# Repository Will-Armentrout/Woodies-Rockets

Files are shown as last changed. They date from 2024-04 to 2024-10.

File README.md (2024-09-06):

# Woodies-Rockets
All files related to rocket design and control\
Created by Will A., Cole D., and Matthew P.\
**How to make a rocket by three college kids** \
Give us a follow at @GoodEnuffEngineering on YouTube, or take the [link](https://www.youtube.com/channel/UCJkPznxXx-ik1TMp3VLUVOw)\
All Scheduling and Daily updates will be listed at the notion linked [here](https://imaginary-cadmium-d3f.notion.site/Woodies-Wockets-60ab52ea17414d15b66bf4899e530979?pvs=4)

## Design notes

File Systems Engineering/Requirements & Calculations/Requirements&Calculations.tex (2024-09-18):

\documentclass[12pt, letter paper]{article}

\usepackage[a4paper, left=0.9in, right=0.9in, top=1in, bottom=1in]{geometry}
\usepackage{graphics}
\usepackage[colorlinks=true, linkcolor=blue, urlcolor=blue]{hyperref}
\usepackage{gensymb}

\title{Requirements and Calculations of a Liquid Rocket Engine}
\author{Will Armentrout}
\date{September 15, 2024}

\begin{document}
	\maketitle

	\tableofcontents
	
	\section{Nomenclature and Terms}
		$ N2O $ - Nitrous Oxide \\
		$ IPA $ - Isopropyl Alcohol \\
		$I_{sp}$ - Specific Impulse\\
		$ O/F $ - Oxidizer/Fuel Ratio
		
	\section{System Requirements/Specifications}
	\begin{center}
		\begin{tabular}{|c |c |c |}
			\hline
			\textbf{Requirement} & \textbf{Value} & \textbf{From?} \\ \hline
			Thrust & 900 N & Rocket Weight \\ \hline
			Specific Impulse & 226 s & NASA CEA \\ \hline
			Tank Pressure & 5.127 MPa & Property (Vapor Pressure: 20 C) \\ \hline
			O/F Mole Ratio & 9 & Ideal Reaction \\ \hline
			O/F Mass Ratio & 6.6 & Calculated (O/F Mole Ratio) \\ \hline 
			Weight Flow Rate & 3.6 N/s & Calculated (Thrust and Isp)\\ \hline
			Mass Flow Rate & 0.4059 kg/s & Calculated (Weight Flow Rate) \\ \hline
			Ox Mass Flow Rate & 0.3525 kg/s & Calculated (Mass Flow Rate) \\ \hline
			Fuel Mass Flow Rate & 0.0534 kg/s & Calculated (Mass Flow Rate) \\ \hline
			Chamber Pressure & 3 MPa & Assumed (Tank Pressure) \\ \hline
			Chamber Temperature & 2966 K & NASA CEA \\ \hline
			Chamber Gas Density & 3.3349 kg/m3 & NASA CEA \\ \hline
			Chamber Gamma & 1.1459 & NASA CEA \\ \hline
			Chamber Mach Number & 0.00 & Assumption \\ \hline
			Chamber SoS & 1015 m/s & NASA CEA \\ \hline
			Throat Pressure & 1.7248 MPa & NASA CEA \\ \hline
			Throat Temperature & 2790 K & NASA CEA \\ \hline
			Throat Gas Density & 2.0577 kg/m3 & NASA CEA \\ \hline
			Throat Gamma & 1.1471 & NASA CEA \\ \hline
			Throat Mach Number & 1.00 & Definition \\ \hline
			Throat SoS & 981 m/s & NASA CEA \\ \hline
			Exit Pressure & 0.1 MPa & Estimated (Altitude) \\ \hline
			Exit Temperature & 1907 K & NASA CEA \\ \hline
			Exit Gas Density & 0.17948 kg/m3 & NASA CEA \\ \hline
			Exit Gamma & 1.2044 & NASA CEA \\ \hline
			Exit Mach Number & 2.708 & NASA CEA \\ \hline
			Exit SoS & 819 m/s & NASA CEA \\ \hline
			Area Ratio & 5.0683 & NASA CEA \\ \hline
			C* & 1487 m/s & NASA CEA \\ \hline
			Specific Gas Constant & 32.4638 g/mol & NASA CEA \\ \hline
			Throat Area & $ 65.591 mm^2 $ & Calculated (Isentropic Equations) \\ \hline
			Throat Diameter & 9.1385 mm & Calculated \\ \hline
			Exit Area & $ 332.4343 mm^2 $ & Calculated (Area Ratio) \\ \hline
			Exit Diameter & 20.5734 mm & Calculated \\ \hline
			Nozzle Exit Angle & 15\degree & Determined (Hobby Rocket Engines)\\ \hline
			Throat Entry Angle & 30\degree & Determined (Youngblood) \\ \hline
			Characteristic Length & 1 m & Determined (Youngblood) \\ \hline
			Chamber Diameter & 30 mm & Determined \\ \hline
			Chamber Length & 84.36 mm & Calculated (Hobby Rocket Engines) \\ \hline
			Chamber Wall Thickness & 5 mm & Calculated \& Determined \\ \hline

		\end{tabular}
	\end{center}

	\section{Derivations, Formulas \& Calculation Process}
		
		\subsection{Deriving Oxidizer/Fuel Ratio}
			Ideal Reaction: 
			$ C_3H_8O + 9N_2O \rightarrow 3CO_2 + 4H_2O + 9N_2 $ 
			\begin{center}
			\textbf{\textit{In reality the reaction is more complicated. the heat of reaction causes many radicals and exotic species that can be calculated but are ignored for simplicity.}} 
			\end{center}
			\noindent Mole O/F Ratio of 9 (9 Moles of N2O for 1 mole of C3H8O). \\
			$ M_{N2O} = 2*14 + 16 = 44 $, 
			$ M_{C3H8O} = 3*12 + 8*1 + 16 =60 $ \\ \\
			$O/F_{Mass} = \frac{9*44}{60} = 6.6 $ (6.6 kg of N2O for 1 kg of C3H8O)
		
		\subsection{NASA CEA}
			Once these variables have been determined the NASA CEA (Chemical Equalibrium with Applications) or other equalibrium solver can be used to get many other critical parameters.
			\subsubsection{Procedure for running the NASA CEA}
				This is by no means the only way to do it. This is also intended as an early design exercise where other chamber pressures and O/F ratios should be analyzed. 
				If you just want a single analysis point don't use the interval tabs and just use the number entry on the right side of the tabs for pressure and O/F ratio.
				\begin{enumerate}
					\item Look up NASA CEA on any browser. URL: \href{https://cearun.grc.nasa.gov/}{\underline{https://cearun.grc.nasa.gov/}}
					\item On the right hand side in the chemical equalibrium problem types check "Rocket". Then hit submit.
					\item On the "Pressure" tab (should be autoselected) enter values for the chamber pressure. 
						\begin{itemize}
							\item This will be based on the tank pressure (5.127 MPa) and the losses in the plumbing to the chamber. 
							\item Since MPa, isn't a selectable option, multiply the MPa number by 10 to get the pressure in bar.
							\item Assume 3 MPa as an approximate starting point. Since 3 MPa is our goal pressure, input 2 MPa (20 bar) as a Low Value and 5 MPa (50 bar) as a high value. 
							\item Make the interval smaller, maybe 0.5 MPa (5 bar) to see a range of pressure values. 
							\item Accept Input and Continue.
						\end{itemize}
					\item On the "Fuel(s)" tab check the "Use Periodic Table (mixtures)" since IPA isn't on the quick select list. Accept Fuel Selection and Continue.
					\item On the "Periodic Table" check Hydrogen, Carbon and Oxygen (as these are the component elements in IPA). Accept Element Selections and Continue.
					\item On the "Select your Fuel(s)" tab check C3H8O, 2propanol (This is the chemical formula and name for Isopropyl Alcohol). Accept Selected Reactant(s) and Continue. 
						There should be a confirmation form, Fuel Mix form and Component Properties form. Accept inputs for all and continue to the next form.
					\item On the "Select your Oxidizer(s)" tab check N2O. Accept Oxidizer Selection and Continue to the next form.
					\item On the "Enter proportions of Oxidizer/Fuel" on the top selection area select Specify with Oxidizer/Fuel Wt. Ratio. 
						\begin{itemize}
							\item We calculated the stoichometric O/F weight ratio earlier as being 6.6. 
							\item If 6.6 is the target value enter a low value of 4 and a high value of 8 and use an interval of 0.2.
						\end{itemize}
					\item On the "Define Exit Conditions" tab define Chamber/Exit Pressure Ratios on the left hand side. 
						\begin{itemize}
							\item In rocket engines the most efficient engine is one that is perfectly expanded (meaning the pressure at the exit of the nozzle is at ambient pressures).
							\item A rocket engine will fly in a multitude of different pressures as it travels upward (pressure decreases with altitude),
								but for now we will analyze with a exit pressure of 1 bar (or about 110m in altitude) as a baseline.
							\item In order to get an exit pressure of 1 bar we take our chamber pressure range (2-5 MPa in steps of 0.5 MPa or 20-50 bar in steps of 5 bar) and divide it by the desired exit pressure.
							\item So for this it's easy. The ratios are just the chamber pressure values. You will have to input each ratio manually (20, 25, 30 ... to 50) on the left column.
							\item Accept Input and Continue to Next Form.
						\end{itemize}
					\item On the "Enter Your Final Choices Before Running CEA" the autogenerated selections should be good (Short, Mass-Fractions, Equilibrium). 
						You can look at your entered ranges for chamber pressure, O/F ratio and chamber/exit pressure ratios before you run the CEA.
						Submit Input and Perform CEA Analysis.
					\item The CEA should run in less than a couple of seconds. The file displayed in the embedded window is the output file. You can download the input and output files in the top right.		
				\end{enumerate}
			\subsubsection{Procedure for analyzing the NASA CEA output}
				The output file of the NASA contains many valuable pieces of information that will be useful in designing a rocket engine later. 
				A navigation tip: the CEA output file is sorted from smallest to largest O/F ratio first and within each O/F ratio it is sorted by chamber pressure. 
				\begin{enumerate}
					\item Scroll through the output file to find the O/F Ratio of 6.6 and the Pin of 3 MPa (435.1 psi). For some reason the CEA output only displays the chamber pressures in psi no matter the input unit.
					\item Once you have found the section where Pin = 435.1 psi and O/F = 6.6 find the exit condition where the P, bar equals 1.000 or Pinf/P = 30. 
						\begin{itemize}
							\item The chamber, throat and exit pressure column where P, BAR = 1.000 (or another exit pressure) are the only columns of interest per section.
						\end{itemize}
					\item Find and record the variables of interest.
						In our case this would be pressure (P), temperature (T), density (RHO), mach number, specific heat ratio (GAMMA), speed of sound (SON VEL), area ratio (Ae/At),
						c star, specific impulse (Isp) and the mass fractions. Here are the values:
						\begin{itemize}
							\item Pressure at the throat: 17.248 Bar
							\item Temperature in the combustion chamber: 2966 K, throat: 2790 K, exit: 1907 K
							\item Density of the combustion gases in the combustion chamber: 3.3349 kg/m3, throat 2.0577 kg/m3, exit 0.17948 kg/m3
							\item Mach Number at exit: 2.708
							\item Specific Heat Ratio at the combustion chamber: 1.1459, throat: 1.1471, exit: 1.2044
							\item Speed of Sound at the combustion chamber: 1015 m/s, throat: 981 m/s, exit: 819 m/s
							\item Area Ratio: 5.0683
							\item C star: 1487 m/s
							\item Specific Impulse: 2218 m/s. In order to convert this to the familiar specific impulse with units of seconds divide by the gravitational constant g = 9.81. $ I_{sp} = \frac{2218}{9.81} = 226 s $
							\item The mass fractions are listed for the main combustion gas products.
							\begin{itemize}
								\item CO: Combustion Chamber - 0.05069, Throat -  0.03951, Exit - 0.00258
								\item CO2: Combustion Chamber - 0.20943, Throat - 0.22700, Exit - 0.28503
								\item H: Combustion Chamber - 0.00010, Throat -  0.00007, Exit - 0.00000
								\item HO2: Combustion Chamber - 0.00003, Throat - 0.00002, Exit - 0.00000
								\item H2: Combustion Chamber - 0.00083, Throat - 0.00065, Exit - 0.00006
								\item H2O: Combustion Chamber - 0.14328, Throat - 0.14690, Exit - 0.15703
								\item NO: Combustion Chamber - 0.01266, Throat - 0.00909, Exit - 0.00047
								\item NO2: Combustion Chamber - 0.00002, Throat - 0.00001, Exit - 0.00000
								\item N2: Combustion Chamber - 0.54681, Throat - 0.54849, Exit - 0.55252
								\item O: Combustion Chamber - 0.00151, Throat - 0.00093, Exit - 0.00001
								\item OH: Combustion Chamber - 0.01160, Throat - 0.00850, Exit - 0.00041
								\item O2: Combustion Chamber - 0.02302, Throat -  0.01885, Exit - 0.00190
							\end{itemize}
						\end{itemize}
				\end{enumerate}
			
		\subsection{Deriving the Flow rates}
			Specific Impulse Equation:  $I_{sp} = \frac{T}{\dot{m} g_0} $ 
			$\rightarrow$
			Weight Flow Version: $ \dot{W} = \dot{m} g_0= \frac{T}{I_{sp}}$ \\
			Solve: $ \dot{W} = \frac{900 N}{226 s} = 3.982 N/s $ \\ \\
			Convert to mass flow: $ \dot{m} = \frac{\dot{W}}{g_0} \rightarrow \dot{m} = \frac{3.9823}{9.81} = 0.4059 kg/s $ \\ \\
			Separate into oxidizer and fuel mass flow rates: \\
			Oxidizer - Nitrous Oxide: $ \dot{m}_{N2O} = \dot{m} * \frac{6.6}{7.6} = 0.3525 kg/s $ \\
			Fuel - Isopropyl Alcohol: $ \dot{m}_{IPA} = \dot{m}*\frac{1}{7.6} = 0.0534 kg/s $ \\
	
	\section{Design Equations}
		\subsection{Nozzle Design Equations}
			\subsubsection{Solving for the specific gas constant}
				The Univeral Gas Constant $ \bar{R} $ is 8.314 J/molK. \\
				The specific gas constant is $ R = \frac{\bar{R}}{M} $ where M is the molecular weight of the mixture of product gases.
				Need to solve for the molecular weight of all of the component gases and their moles in mass fraction.
				\begin{itemize}
					\item CO: $ M = 12 +16 = 28 $ $x_{CO} = 28 \cdot 0.03951 = 1.1063 $ moles
					\item CO2: $ M = 12 + 16  + 16 = 44 $ $ x_{CO2} = 44 \cdot 0.2270 = 9.988 $ moles
					\item H: $ M = 1 $ $ x_{H} = 1 \cdot 0.00007 = 0.00007 $ moles
					\item HO2: $ M = 1 + 16 + 16 = 33 $ $ x_{HO2} = 33 \cdot 0.00002 = 0.00066 $ moles
					\item H2: $ M = 1 + 1 = 2 $ $ x_{H2} = 2 \cdot 0.00065 = 0.0013 $ moles
					\item H2O: $ M = 1 + 1 + 16 = 18 $ $ x_{H2O} = 18 \cdot 0.1469 = 2.6442 $ moles
					\item NO: $ M = 14 + 16 = 30 $ $ x_{NO} = 30 \cdot 0.00909 = 0.2727 $ moles
					\item NO2: $ M = 14 + 16 + 16 = 46 $ $ x_{NO2} = 46 \cdot 0.00001 = 0.00046 $ moles
					\item N2: $ M = 14 + 14 = 28 $ $ x_{N2} = 28 \cdot 0.54849 = 15.3577 $ moles
					\item O: $ M = 16 $ $ x_{O} = 16 \cdot 0.00093 = 0.01488 $ moles
					\item OH: $ M =16 + 1 = 17 $ $ x_{OH} = 17 \cdot 0.0085 = 0.1445 $ moles
					\item O2: $ M =16 + 16  = 32 $ $ x_{O2} = 32 \cdot 0.01885 = 0.6032 $ moles
					\item Total: $ x_{total} = 1.1063 + 9.988 + 0.00007 + 0.00066 + 0.0013 + 2.6442 + 0.2727 + 0.00046 + 15.3577 + 0.01488 + 0.1445 +0.6032 = 30.1346 $ moles
				\end{itemize}
				Molecular weight of mixture is $M = 28 \cdot \frac{1.1063}{30.1346} + 44 \cdot \frac{9.988}{30.1346} + 1 \cdot \frac{0.00007}{30.1346} + 33 \cdot \frac{0.00066}{30.1346} + 2 \cdot \frac{0.0013}{30.1346} + 18 \cdot \frac{2.6442}{30.1346} + 30 \cdot \frac{0.2727}{30.1346} + 46 \cdot \frac{0.00046}{30.1346} + 28 \cdot \frac{15.3577}{30.1346} + 16 \cdot \frac{0.01488}{30.1346} + 17 \cdot \frac{0.1445}{30.1346} + 32 \cdot \frac{0.6032}{30.1346} = 32.4645 g/mol$ \\ \\
				Solve for specific gas constant $ R = \frac{8.314}{32.4645} = 0.2561 J/gK = 256.1 J/kgK $ 

			\subsubsection{Throat Area}
				Mass Flow Rate at the throat: $ \dot{m} = A_t \frac{P_o}{\sqrt{T_o}}\sqrt{\frac{\gamma}{R}} (\frac{\gamma + 1}{2})^{\frac{\gamma + 1}{2(1-\gamma)}}  $ \\
				Area of Throat: $ A_t = \frac{\dot{m}\sqrt{T_o}}{P_o}\sqrt{\frac{R}{\gamma}} (\frac{\gamma + 1}{2})^{\frac{\gamma + 1}{2(\gamma -1)}}$ \\ \\
				Values used in the Equation: \\
				Mass Flow Rate $ \dot{m} = 0.4059 kg/s $ \\
				Stagnation Temperature $ T_o = T_{chamber} = 2966 K $ \\
				Stagnation Pressure $ P_o = P_{chamber} = 3 MPa $ \\
				Gamma (at the throat) $ \gamma_{throat} = 1.1471 $ \\
				Specific Gas Constant (at the throat) $ R_{throat} = 256.1 J/kgK $ \\ \\
				Plug in the numbers: $ A_t = \frac{0.4059 \cdot \sqrt{2966}}{3 \cdot 10^6}\sqrt{\frac{256.1}{1.1471}} (\frac{1.1471 + 1}{2})^{\frac{1.1471 + 1}{2(1.1471 -1)}} = 6.5591 \cdot 10^{-5} m^2$ \\ \\
				Solve for Diameter $ A_t = \pi \frac{{D_t}^2}{4}  \rightarrow D_t = \sqrt{\frac{4A_t}{\pi}} = \sqrt{\frac{4 \cdot (6.5591 \cdot 10^{-5})}{\pi}} = 0.0091385 m = 9.1385 mm$
			
			\subsubsection{Exit Area}
				Use the throat area and determined $ A_e/A_t $ to get the exit area. $ \frac{A_e}{A_t} = 5.0683 $ \\
				$ A_e = 5.0683 \cdot 6.5591 \cdot 10^{-5} = 3.3243 \cdot 10^{-4} m^2$ \\
				Diameter: $ D_e = \sqrt{\frac{4 A_e}{\pi}} = \sqrt{\frac{4 \cdot(3.3243 \cdot 10^{-4})}{\pi}} = 0.02057 m = 20.5734 mm $ \\
			
			\subsubsection{Nozzle Angles}
				In normal commercial rocket engines the nozzle angle is optimized so that when the flow leaves it is as 1D as possible, to achieve max thrust. 
				The profile that maximizes thrust for a certain throat area and length is called an "Rao optimum contour". This is is named after G.V.R Rao and is complicated to manufacture. 
				Because of its complexity we will just use a 15{\degree} conical nozzle profile, common for hobby and small area ratio engines. It has 98.3\% of the performance of an ideal nozzle, so close enough for me.

		\subsection{Combustion Chamber Equations}
			
			\subsubsection{Chamber Length}
				For the combustion chamber Hobby Rocket Engines references a combustion chamber with a cross sectional area of at least 3 times the throat area. 
				For this reason we choose a chamber diameter of 30 mm, much larger than the required size, subject to change based on the injector. \\ \\
				The chamber volume required for complete combustion is defined by the characteristic chamber length: $ L^* = V_c/A_t \rightarrow L^* A_t = V_c $ where $ V_c = A_c L_c +$ convergent volume  \\
				Youngblood references a characterisitc length of 1m being successful in nitrous, ethanol engines so that value will be used as a minimum. \\ \\
				For small combustion chambers the convergent volume is 1/10th the cylindrical portion so $V_c = 1.1A_cL_c $ \\
				Combine Equations $ L^* A_t = 1.1A_cL_c \rightarrow L_c = \frac{L^* A_t}{1.1A_c} = \frac{(1) (6.5591 \cdot 10^{-5})}{1.1(\pi \frac{0.03^2}{4})} = 0.08436 m$ or $ 84.36 mm $
			
			\subsubsection{Chamber Thickness}
				This system will definitely not be thin walled but it is a good starting point for minimums. \\
				The axial or longnitudinal stress in a thin walled pressure vessel is given by the equation: 
				$ \sigma_a = \frac{Pr}{2t} $ Where P is the pressure, r is radius and t is the thickness. \\ \\
				Rrearrange for thickness: $ t = \frac{Pr}{2\sigma_a} $ In our case pressure is the chamber pressure (3 MPa), radius is 15 mm and sigma is material dependent. 
				Since steel is cheap we will use that, heat transfer be damned (hopefully we don't run it for long enough). Steel rod stock on McMaster has a tensile yield stress of 60,000 psi or 413.685 MPa. \\
				Plug this in:  $ t = \frac{3 \cdot 15}{2 \cdot 413.685} = 0.054389 mm $ 
				Remember this number is at ambient temperatures and the combustion chamber gas were calculated to be at 2966 K (Above the melting point of steel). \\ \\
				Recalculating with an operating temperature of 500{\degree}C or 773.15 K steel has about 40\% of it's yield strength at 21C. Using this: $ t = \frac{3 \cdot 15}{2 \cdot(0.4) (413.685) \cdot} = 0.13597 mm $ \\
				Not really much of a worry, but let's use something thick enough to handle the heat loads as well, call the wall thickness 5mm.

\end{document}

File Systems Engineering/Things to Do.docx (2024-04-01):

# Things to Do

1. Determine Thrust, Specific Impulse, Flow Rate
2. Propellant Determination
  a. Stoichiometric Ratio
3. Run CEA
  a. Get O/F
  b. Combustion Temperature
  c. Exit Velocity
  d. Area Ratio
  e. Combustion Pressure
  f. Gamma
4. Design Nozzle and Combustion Chamber
5. Research Injector Types, Determine optimal injector design.
6. Design Injector Plate
7. Flow Diagram
  a. Determine Fuel/Ox and Backfill Gas Tanks
  b. Gas Hose
  c. Valves
  d. Connectors
  e. Gauges
8. Design a Test Stand
  a. Aluminum Extrusion
  b. Force Transducer
  c. SAFETY
9. Find a place to test this.
10. Test

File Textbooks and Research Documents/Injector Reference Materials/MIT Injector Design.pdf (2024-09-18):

Created by Unknown User (ahodge@mit.edu), last modified by Amir J White on Jul 07, 2022 18:22

# Topic 6: Injector Design

Return to Learning Curriculum

# LS6: Injector Design

### Lecture Zoom Recording

Original Authors: John Posada '24, jposada@mit.edu & Max Kwon '22, mawkwon@mit.edu

Note: This LSET is pretty long so check the summary at the bottom of this page if you'd prefer an abridged version Great links (for the giga-nerds)
General resources
Wikipedia
Pyralis cold flow test (shoutout to our ancestors) More advanced resources -- skip for now
Huzel & Huang the bread and butter of liquid prop

### 4.5 Injector Design

That one NASA paper

### 2.1 Injector Flow-System Geometry

But particularly 2.1.1.1 Total Element Pattern
Rocket propulsion elements textbook
This paper on pintle injectors
We use a pintle injector on the upcoming Romulus engine if you’d like to learn more!

## What is an Injector?

The injector is a critical part of a liquid rocket engine (abbr. LRE) that is located between the upstream feed system and the combustion chamber. It is designed to inject the propellants (fuel/ox) from the feed system into the combustion chamber in a way that ensures three main things for the engine:

### 1. It optimizes the flow and the impingement of the propellants for optimal combustion

a. Optimal flow → better fuel efficiency (less uncombusted propellant)
b. Optimal combustion → better engine performance (more thrust)

### 2. It ensures that the combustion is stable for the entire time the engine is fired

3. It helps preserve the structural integrity of the combustion chamber and the engine itself
a. Mostly by ensuring that the resulting combustion temperature does not melt the chamber walls

Piping the propellants directly into the combustion chamber without a proper injector would be disastrous for the engine’s mission because none of these points above would be satisfied.

You can think of the injector as the interface between the feed system, which supplies the propellants at certain mass flow rates, pressures, etc; and the combustion chamber, which requires certain performance metrics, pressures, temperatures, etc.

Below is a diagram of the design for the Helios injection system:

Topic 6: Injector Design - MIT Rocket Team - MIT Wiki Service | https://wikis.mit.edu/confluence/display/RocketTeam/Topic+6%3A+Inj...
1 of 14 | 9/18/2024, 1:19 PM

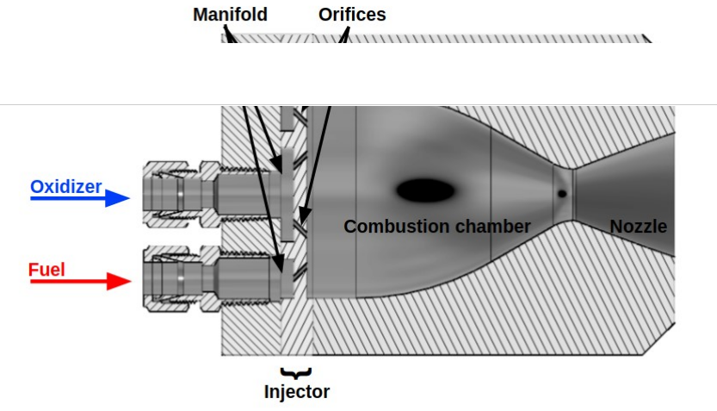
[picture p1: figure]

This design, unlike the doublet impinging jet design (discussed later), is relatively simple: it simply angles the fuel and oxidizer streams towards each other and slams them together really fast. Below is an image of the actual Helios injector (from a top-down view, as if you are the feed system):

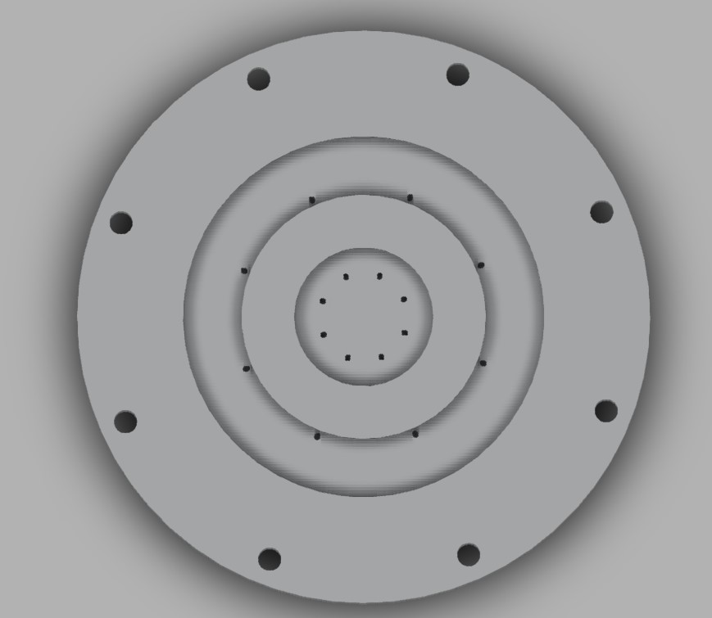
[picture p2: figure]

The inner circle and outer ring groove are known as manifolds (discussed later), and the two sets of orifices for the propellants are seen in either of these manifolds. The outermost ring of large holes is just the bolt holes for securing the injector onto the engine.

The magic in the design is the precise hole diameters, angles, and lengths that ensure optimal flow behavior during firing. In addition, more considerations, like which propellant to inject through the centermost manifold, the shape of the manifold, and the number of orifices are very important in the design of this kind of injector. This video shows a cold flow test (water-only) of another style of an impinging jet design.

For those familiar with liquid engines in other types of vehicles, you’ll know that many mix the propellants before combusting them in order to optimize the combustion. In many general aviation aircraft engines and older car engines, you’ll find this premixer is the carburetor. In contrast, premixing in liquid rocket engines is usually not advisable because of the volatility of the propellants, and so ensuring optimal mixing inside the combustion chamber is also a task for the injector. However, do note that in some advanced rocket engines (like SpaceX’s Raptor!), premixing before entering the combustion chamber is a thing that can be done.

## Injector Performance

Before we get into the more specific aspects of injector design, it would be good to first understand what principles and metrics we’re trying to satisfy with the injector. Also, throughout the design process, you’ll often want to assess how ‘good’ your injector actually is at doing its job. But how do we evaluate this?

There are a few general metrics and areas that we should always take into consideration to try and evaluate both whether our design does

2 of 14 | 9/18/2024, 1:19 PM

relatively well and whether the design will work within the rest of our engine’s physical constraints. Of course, there will typically be even more metrics used in the research literature for different injector designs, which should also be considered but are not covered here.

### Mixing & Atomization

We’re going to mention these words a lot in this LSET. Mixing refers to the actual mixing of the different propellants into a local solution. The better 2 propellants mix, the better they can chemically react when they combust. Atomization refers to the breakup of a flowing propellant stream into individual droplets. This is important because smaller droplets both promote mixing (by allowing space for the other propellant to mix), and vaporization (since it’s energetically easier for a droplet to convert to vapor than an entire stream of fluid).

### Droplet Size

This is the ‘measurable version’ of atomization, and a metric we try to minimize. In practice, this is a very difficult thing to actually measure since you’d have to capture images inside the combustion chamber during injection, and because the droplet sizes differ over time, between propellants, and within a single propellant. For the metric, what we do is use one of a number of measurements that tries to capture the ‘average droplet size’. A popular choice among them is the Sauter mean diameter (search it up if you’re curious but don’t think too hard about it).

But how would we find it, anyway? In some cases, we can estimate the droplet size using published empirical formulas (based on the chosen injector design/flow characteristics). We can also use computational fluid dynamics methods (abbr. CFD) to computationally model the flow and estimate it that way. CFD is a little difficult to learn and use properly, though, but it is a very popular tool for verifying flow characteristics.

### Impingement Distance

The impingement distance can be defined as the axial distance the propellant travels before impinging with the other propellant. This is an important metric because it tells you at about what point in the combustion chamber you can expect most mixing to begin, and subsequently, a general idea of after where combustion will happen, which is good to know for thermal analysis and making sure your injector doesn’t melt.

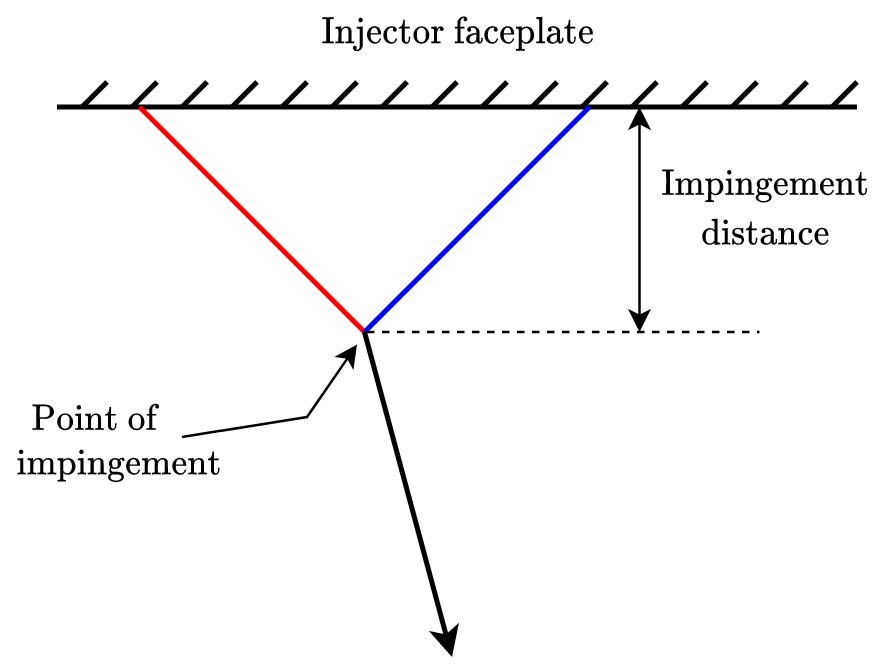
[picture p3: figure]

There’s no real desire to have it very close to the injector (which can unnecessarily heat the faceplate) or to have it very far from the injector (which means your combustion chamber will have to be even longer). There are some rules of thumb found in the literature for what impingement distance you should aim for based on your injector type, and they are usually measured relative to the diameter of the orifices in the injector.

### Vaporization Length

For the most part, the actual combustion inside an LRE occurs in the gas phase, which is why we want our liquid propellants to mix well before they vaporize so that they can combust more efficiently. The term vaporization simply refers to this conversion from liquid to gas in the propellants as they heat up inside the combustion chamber.

Vaporization length is a rough estimate of how far it’ll take either propellant to travel within the chamber before they vaporize (and thus do the bulk of their combustion). Like droplet sizes, the most that can typically be done is to use a published empirical formula to try and find the vaporization length, then verify this using CFD.

### Combustion Stability

This is quite a deep and pretty complex subject that has so much to cover, so we only give a general gist of it here. While the rocket engine is being fired, there are always unavoidable and pretty random chamber pressure fluctuations. If your entire system is designed well, these fluctuations appear just like low magnitude random noise and don't cause a problem. Typically, up to a 5% fluctuation in chamber

3 of 14 | 9/18/2024, 1:19 PM

pressure is permissible (peak to peak pressure), but there are some cases where this threshold must be reduced further.

However, if these pressure fluctuations exhibit a different kind of behavior, it can be disastrous for your system. One common occurrence in unstable combustion is resonance (a phenomenon you might remember from high school physics), whereby these small pressure fluctuations build up additively over time to really destroy your system.

We bring this up because the injector is one of the most influential parts of a rocket engine when it comes to the stability of combustion. We won’t cover here specifically how, but know that the design, and particularly the orifice pattern, of the injector plays an important role in stability, but can come at the price of having to compromise combustion performance and efficiency. In addition, there are some physical structures that can be added to the injector that can help mitigate combustion instabilities (namely baffles and acoustic cavities), but we won’t cover those here.

## Common Injector Types

Of course, there is not a single injector design that is best for any liquid rocket engine. Choosing which injection scheme to use depends on the objectives of the mission, experience of the design team, machining limitations, and other factors that must all be considered by the team before beginning development.

Here we cover 3 common types of designs used in liquid rocket engines, but there are many other types and variations to these that can be developed depending on what is needed for the engine.

### Non-impinging Shower Head

Just kidding – before we get into designs that are used today, here’s a design that is actually no longer used at all (because history is cool). It simply injects the propellants axially straight into the combustion chamber.

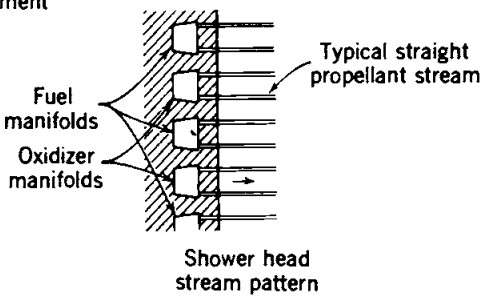
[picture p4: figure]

This design was used in the German V-2 rocket and relies on turbulence and the propellants diffusing in order to achieve proper mixing and combustion. It is the simplest non-impinging design but is no longer used because it requires a very large combustion chamber volume to work properly, and other designs are simply better. The following designs are currently widely used in liquid rocket engines.

### Impinging Jet

Perhaps the simplest of these, the impinging jet design is simply sets of angled orifices that slam the two propellants together really fast (known as impinging them).

For these, there are considerations like hole diameters, angles, lengths, number of holes, spacing of holes, etc. It is very important to know the point and angles of impingement so that you can make sure you’re not combusting directly onto the chamber wall and melting it.

The primary advantage of this design is its simplicity, which speeds up the design process considerably, and allows the team to machine the injector relatively quickly.

### Like/Unlike Impinging Jet

4 of 14 | 9/18/2024, 1:19 PM

For this design, you can choose to either impinge two like propellants (fuel on fuel, oxidizer on oxidizer) or two unlike propellants (fuel on oxidizer).

Like impinging jets (also known as self-impinging) allow the separate propellants to atomize very well and break up into very small droplets, and result in fan streams that then mix the two propellants for combustion.

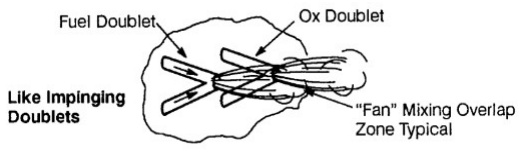
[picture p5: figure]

Unline impinging jets allow the two propellants to mix very well. As a note, unlike impinging jet designs are quite popular when the oxidizer is liquid oxygen (LOX), but the tradeoff is that it is relatively less stable than other common injector designs, and so combustion stability becomes a design concern.

Doublets/Triplets/etc.

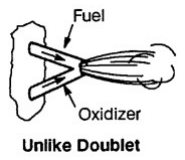
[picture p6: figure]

It may also be beneficial to increase the number of streams impinging at a single point from 2 to 3 or more.

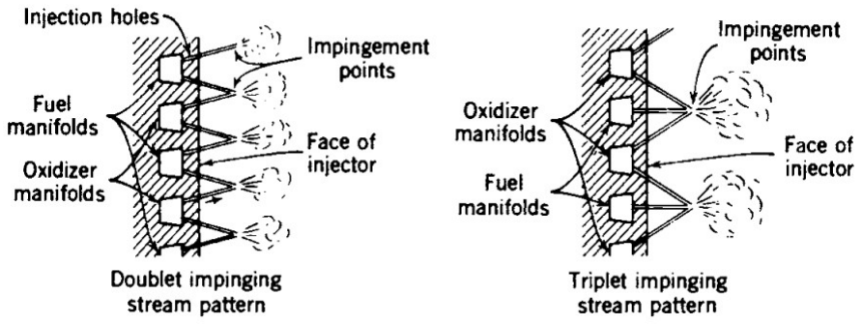
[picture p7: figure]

This design can help when there is a mismatch in the fuel and oxidizer stream momentums, which may result in an unfavorable resultant angle (e.g. that could spray flames towards the chamber wall instead of the nozzle exit). Additionally, increasing the amount/momentum of propellant impinging generally also improves the mixing of the propellants.

## Pintle

The pintle injector design typically consists of just one element and works by impinging a central radial flow with an outer axial flow as shown below.

5 of 14 | 9/18/2024, 1:19 PM

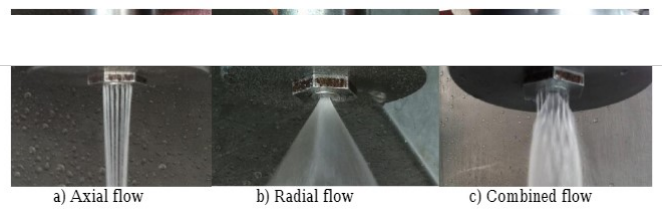
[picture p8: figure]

The injector gets its name from the pintle-shaped bit (that green knob thing on the far right of the figure below) that allows the central flow (the red below) to turn from going towards the nozzle exit to spraying radially, more towards the chamber walls. It then impinges directly onto the outer flow (the blue below) which is going axially down the chamber. The result of their combined flow is a cone of liquid film. →

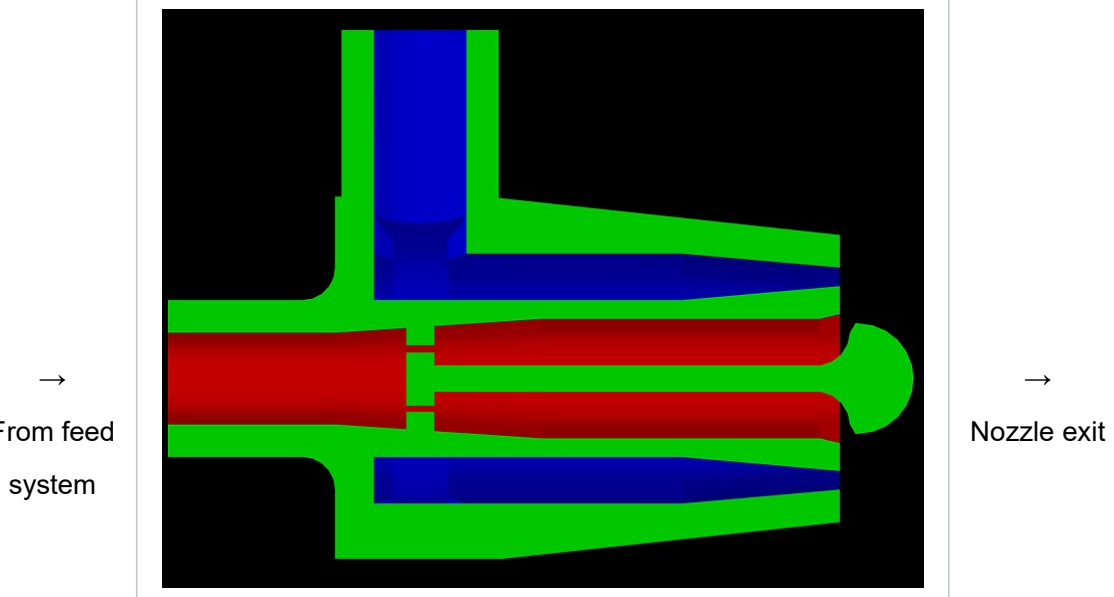
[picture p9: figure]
system; Nozzle exit

From feed

The pintle injector is a popular injector choice because it’s not incredibly complex, and provides a few notable advantages:

Improved mixing caused by the very sharp angle of impingement, and non-planar impingement area
Lots of freedom in design choices – namely, it’s relatively easy to introduce orifices whose opening area can be changed allows the engine to be throttled (changing how much propellant we are injecting, which allows us to control thrust output)
There has been observed combustion stability inherent to the pintle design

A few theories exist to explain this inherent combustion stability, but it is most likely due to two things: the pintle’s central position in the chamber, and its recirculation zones. These recirculation zones are an important characteristic of pintle injectors and are where uncombusted propellants form (their own respective) loops in the chamber. Here, they deflect the incoming flow, and depending on the thermal profile, can either heat or cool the pintle tip and the chamber walls (it’s kinda complicated!).

6 of 14 | 9/18/2024, 1:19 PM

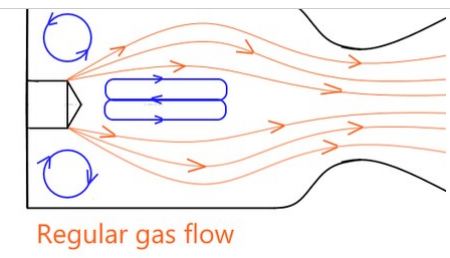
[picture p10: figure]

The first theory explains that the central pintle is located at a nodal point within the chamber’s acoustic pressure field (you don’t need to know what this means!), and so energy released at the pintle tip doesn’t contribute very much to the pressure fluctuations that cause combustion instabilities. The second theory suggests that the recirculation zones act as a sort of ‘damping zone’ for possible instabilities arising from the combustion gases.

Of course, no design has only advantages. The pintle injector design can be susceptible to undesirable heating both on the pintle tip itself and on the chamber walls. As such, the pintle injector is often complemented by a dedicated cooling system (like regenerative cooling or film cooling!).

### Coaxial Swirl

The coaxial swirl injector, as the name suggests, uses two coaxial tubes (called swirlers) that swirl their propellants. Once either propellant exits its swirler, it sprays into a cone of liquid film. Depending on the desired behavior, the cones can be made to collide with each other before reaching the chamber wall or not. Check out this video to see a cold flow test of a coaxial swirl injector.

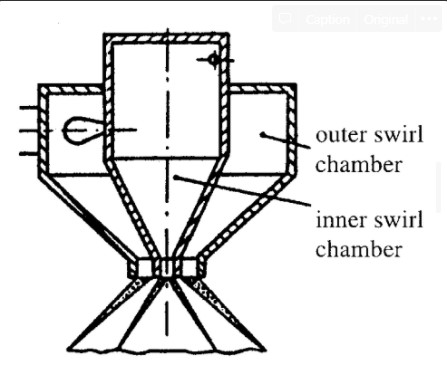
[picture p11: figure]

The primary advantages of a coaxial swirl design are:

Relatively stable across a large range of mass flow rates, allowing for higher mass flow rates than other designs
This is because the mixing and atomization processes that occur in the chamber are less sensitive to any pressure fluctuations or flow velocity variations with this design since pressure oscillations within the swirling flow itself help stabilize external oscillations
Don’t worry if that doesn’t make much sense!
Better atomization of propellants in the cone sheets leads to smaller droplet sizes which also allows for better mixing
Also, the swirling gives the propellants radial, in addition to axial, momentum, meaning they have more time to mix when they enter the chamber
7 of 14 | 9/18/2024, 1:19 PM

Reduced worry of combustion instabilities

On the other hand, this design is not good for very viscous propellants because of the behavior of the swirlers, which reduces the atomization of these kinds of propellants. In addition, modeling the flow behavior inside the swirlers can become quite complex, especially in the inner swirler because of the presence of a central gas core that forms as the propellants swirl around.

Inner/External Mixing

A lot of design choices can be made that affect the overall behavior of this type of injector. One of the major choices is choosing whether to design for inner or external mixing.

External mixing is when the inner and outer cones are able to exit directly into the combustion chamber and mix that way.

Internal mixing is when the outlet for the inner swirler is recessed far back enough such that the inner cone collides with the wall of the outer swirler, pictured to the right.

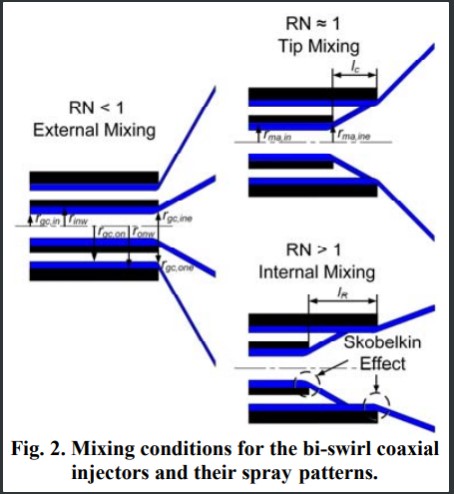
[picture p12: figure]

This choice primarily affects the flow behavior (internal mixing can be more difficult to model), and the resultant angle, but there isn’t very much research to back up giving a more specific description than this.

One final note: researching the coaxial swirl injector can be very difficult because a lot of the work on this type of injector was done by Soviet rocket engineers, and most of their records are no longer available or were simply never published. For this reason, you’ll find conflicting information and many different names referring to the same thing (e.g. coax swirls are also known as bi-swirl coax, duplex, double simplexes, etc.). On the other hand, it has been used previously by NASA and notably by SpaceX’s Raptor engine, so information might be found through their organizations.

### Non-primary Injection

This is a very general class of injection that typically involves just designing holes or slots that serve a different purpose than the primary injector. Typically these are non-impinging holes implemented for cooling purposes within the chamber.

The most common of these is called film cooling. This is when some of the fuel or oxidizer is diverted from the main flow and injected almost parallel onto the walls of the combustion chamber. This forms a protective film of coolant along the chamber wall, which helps keep the chamber wall cool, as illustrated below.

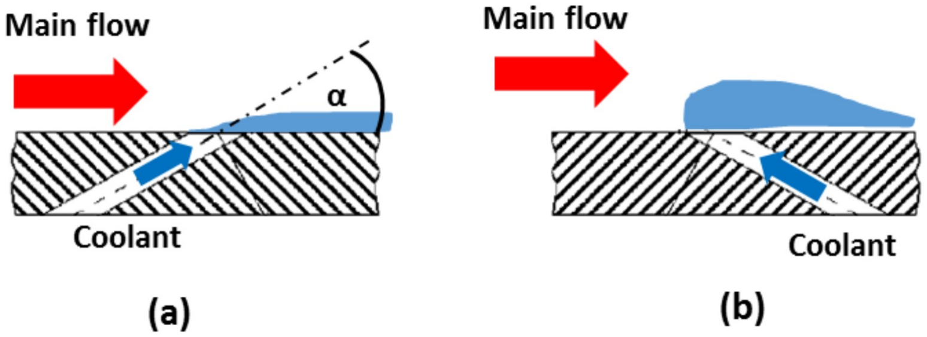
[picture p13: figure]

## Upstream of the Injector

8 of 14 | 9/18/2024, 1:19 PM

What occurs upstream of the injector is very important to the design of the injector. Before the propellants enter the injector, several properties must be known in order to properly develop the geometry of the injector.

## Feed System Inputs

From the feed system, we must know the mass flow rate of both propellants, the total drop in pressure from their initial reservoir pressure, and the actual properties of either propellant (density, boiling point, etc.). It’s useful to be very familiar with the actual behavior of the fluids, and knowing how, for example, the viscosity may play a role in the injection of the propellants can be critical.

Knowing the feed system inputs allows us to determine the desired aspects of the injector from the desired outputs of the entire engine – remember, think of the injector as the interface between the feed system and the rest of the engine.

Among the most important outputs of the system are the resulting mass flow rates, the pressure drop, and the vaporization length.

A good rule of thumb for initial injector design is that the drop in pressure across an orifice be 20% of the chamber pressure (we discuss more on how to design for this later). This is also referred to as the stiffness of the injector. The relatively large difference in pressure forcefully pushes the propellants through the orifices with high velocity, which is vital to combustion stability. Without that high velocity out of the orifice, the propellants could be subject to flow dribble, where they tend to pool up at the orifice exit, causing poor mixing and hindering the flow into the chamber.

Pressure drop and flow rates also have some effect on combustion stability, but that’s a very difficult topic that we won’t cover very much here.

### Manifold

The manifold is a space that properly reroutes the feed system propellant flow into the injector. It can also be thought of as an interface – this time between the feed system and the injector orifices. Below is a diagram of the Pyralis injector, with the fuel manifold in orange and the oxidizer manifold in green.

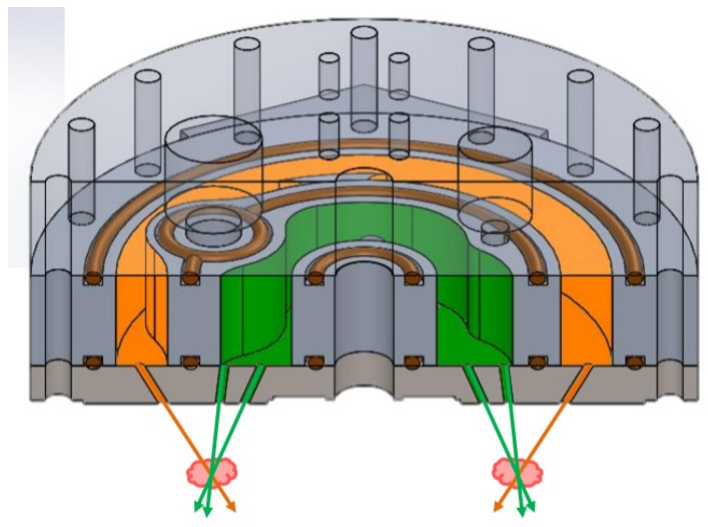
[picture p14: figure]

These spaces are specifically designed to evenly distribute the propellants across the face of the injector, allowing them to flow properly through the orifices. The manifold can also be vital for changing some aspects of the flow. For example, introducing a constriction in the manifold (called a venturi) is often used in pintle injectors to speed up the flow before it exits the orifices.

An important consideration for both manifold and injector design is whether to have the fuel or the oxidizer be the centermost propellant on the face of the injector. This decision has 2 consequences:

1. Any central propellant that does not directly impinge with the other propellant will go on to collide directly with the chamber wall.
a. Typically, the oxidizer is at a lower temperature than the fuel (most of the time, the oxidizer is cryogenic LOX). This allows us to use that unimpinged propellant as an auxiliary coolant for the chamber walls.
2. The outer propellant must be routed to the injector and comes in contact with more surface of the material used to make the injector.
a. If this outer propellant is LOX, we have to make sure that this material is compatible with LOX. Most materials are not compatible with LOX, which means it could cause problems like autoignition (very bad!!).
i. This is doubly so if the outer propellant is used for regenerative cooling because then it must flow through the entire length of the chamber, and so the entire chamber would have to be rated for LOX as well.

As such, we typically design manifolds as ox-centered, but this is not always the case.

9 of 14 | 9/18/2024, 1:19 PM

## Injector Geometry

It’s difficult to give a general overview of the geometry of the injector because it varies from design to design, but there are a couple of key principles that mostly apply to all kinds of injectors. If you begin to work with injectors more closely, you’ll find more detailed design procedures and metrics that you need to account for depending on the design that you choose.

### Number of Elements/Orifices

The term element usually refers to the independent set of things that make up a unit of the injector, and varies from design to design. For example, in an impinging jet doublet, a pair of holes is an element, while in a coax swirl, the entire structure is an element.

You can have more than one element, and in some cases, like the impinging jet designs, you will have several of these. Deciding how many elements your injector will have is important because it directly affects the output of the injector (in terms of mass flow, propellant spread, etc.), but also can change other aspects of the geometry of each element.

The main consideration for each element is the size of its orifices. In general, the term orifice refers to a hole, but can also refer to a slot, annulus, or any general ‘exit’ for the propellant into the combustion chamber. Having more elements typically requires each element to have smaller orifices in order to supply the same mass flow, as you will see below.

### Sizing

The sizing of orifices in an injector element typically comes from knowing the desired mass flow rate ṁ out of that orifice and the desired pressure drop ΔP across that orifice. Using the equation below, we can find A, the area needed for that orifice.

The two other variables, Cd and ρ, are the coefficient of discharge and the density of the fluid going through the orifice, respectively.

The coefficient of discharge is a nondimensional number that tells us what fraction of mass flow going through an orifice actually ‘gets through’. We can define it as the ratio of actual mass flow to theoretical mass flow out the end of an orifice, and so is between 0 and 1. We usually take an empirical estimate of this number based on the shape of the orifice (e.g. sharp corners experience more flow loss than round corners, so have a lower Cd, illustrated below).

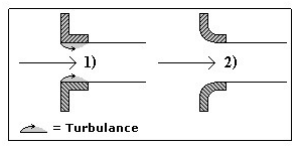
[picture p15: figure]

This equation can also be used in reverse, taking a given area (or diameter of hole) and finding the resulting mass flow through that orifice. This can be very useful if there are hard-set manufacturing limits, and is also useful for designing non-primary injections.

In general, a larger number of smaller holes will result in more spread of your propellant and allow for better mixing and atomization throughout the combustion chamber.

Knowing this, you might wonder why we don’t just use a very large number of very small holes to achieve the best performance. In fact, if all we cared about was engine performance, we would! The reason we don’t is that we also have to make the engine ourselves, and choosing to design such precise and difficult-to-machine parts is incredibly tedious and, in some cases, impossible.

As such, always be mindful of the actual manufacturing of the injector when sizing it. Oftentimes, the part will be machined by hand, and you don’t want to be the reason someone is stuck drilling 70 very precise 0.5 mm holes the night before their midterm (and you certainly don’t want to be that person yourself!).

And another note, having a relatively large number of orifices can bring up even more concerns regarding combustion stability, due to more fine patterns causing more unstable energy/pressure fluctuations, but that’s not a topic we’ll delve into very deeply.

### Angles

There are 2 important angles to keep track of in the design of the injector: the angle at which the propellant enters the combustion chamber,
and the resultant angle of the fluids after impingement. Knowing the entry angle can typically get you a very good idea of the resultant angle
10 of 14 | 9/18/2024, 1:19 PM

if you also know the momentums of the two streams.

Knowing the resultant angle is critical because you want the fluids to combust axially downwards, towards the nozzle exit, and not towards the chamber walls. In some cases, it is sufficient to use this equation, derived from basic collision kinematics (from high school physics!), to find the resultant angle,

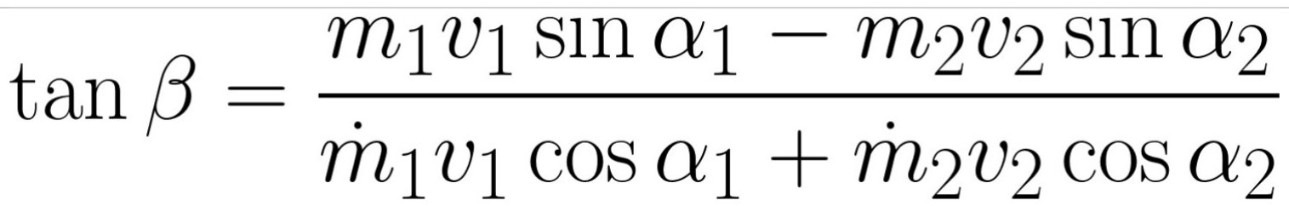
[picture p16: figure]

Where ṁ is the mass flow rate, v is the velocity, the subscripts 1 and 2 refer to either propellant, and the angles are illustrated below.

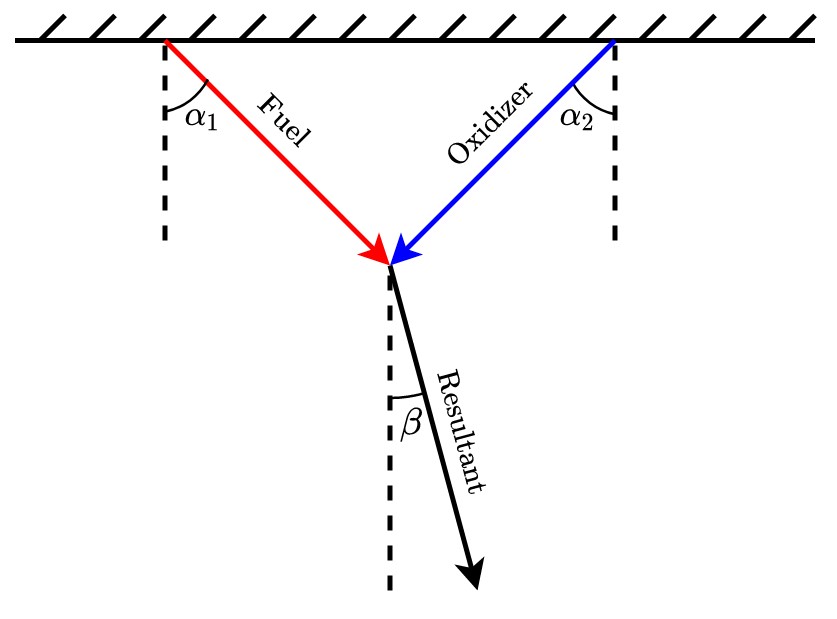
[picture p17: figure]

In general, you want the resultant angle to be very close to zero (i.e. going straight down the chamber towards the nozzle exit). Note that we have to use ṁv, the fluid’s momentum per second (units Newtons) because the flow is a moving continuous mass.

Sometimes, though, this approximation does not match empirical data, like with pintle injectors (among other designs or variations). In these cases, there are often published empirical formulas that can be used to acquire a better approximation of the resultant angle.

### Orifice Length

The actual length of the orifice, from entry to exit, is actually an important factor in determining the behavior of the fluid flow across the injector. What we want is an orifice long enough to avoid flow separation, a phenomenon we won’t really discuss but just know that it can amplify flow losses – when the flow loses energy (and thus is slower, and can sometimes cause even more problems at the orifice exit or within the stream flow into the chamber). In addition, ensuring the orifice is an adequate size helps us also better avoid the problem of flow dribble that we mentioned earlier.

Most literature agrees that a good rule of thumb (at least for simple impinging jet orifices) is that the ratio of the orifice length to the orifice diameter (its L/d) should be at least 5. Having slightly less than this is sometimes ok, but it’s best to aim for at least that, and not have an incredibly long orifice.

# Summary

If you remember nothing from above, or just don’t wanna read all that, at least remember these points!

The injector is a part of the liquid rocket engine located between the feed system and the combustion chamber
Its job is to inject the propellants (fuel/oxidizer) from the feed system into the combustion chamber in a way that Optimizes the flow/impingement → optimizes combustion
Ensures combustion stability
Makes sure the chamber walls don’t melt
11 of 14 | 9/18/2024, 1:19 PM

Check out this video of a cold-flow test of a simple injector

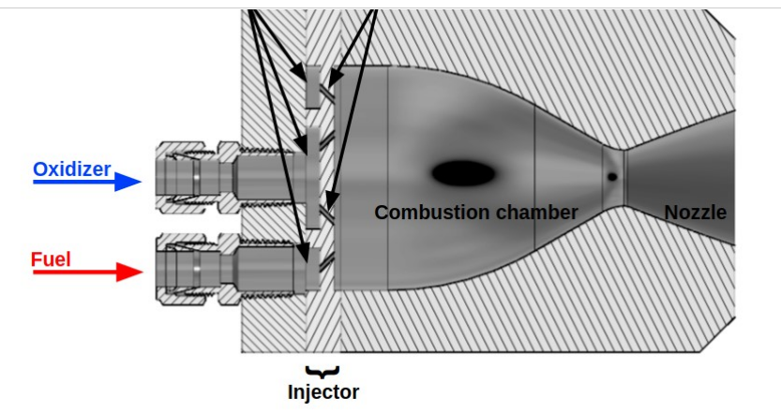
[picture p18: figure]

Mixing is the mixing of two different propellants into a local solution
The propellants need to be well-mixed in order to combust effectively
Atomization is the breakup of a single propellant stream into individual droplets
Promotes vaporization, since it requires less energy to turn a single droplet into a vapor than an entire stream of fluid This can be measured by a metric of ‘average droplet size’, and we want to minimize this, if possible
Very commonly used as a metric of ‘average droplet size’ is the Sauter mean diameter
Vaporization is the conversion of liquid propellant into a vapor
Most of the combustion in a liquid rocket engine occurs in the gas phase
It’s critical that vaporization finishes before the propellants reach the end of the combustion chamber, and is measured using vaporization length
The 3 common types of injectors we looked at were:
Impinging jet: simply injects the propellants through angled orifices so they slam into each other really fast

Very simple to design, but combustion can be unstable

Like impinging (fuel on fuel, ox on ox) is good for atomization

Unlike impinging (fuel on ox) is good for mixing

Unlike doublets are used in our Helios engine!

Pintle: injects one propellant straight down the chamber, and the other radially

12 of 14 | 9/18/2024, 1:19 PM

Relatively simple, better
mixing

Characteristic recirculation zones where uncombusted
propellant loops back
around in the chamber

Contributes to
combustion
stability, cooling,
and heating

Used in our Romulus
engine!

Coaxial swirl: swirls the two propellants in coaxial swirl chambers down towards the chamber, and injects the resulting cones of liquid film

Some stability, better atomization

Pretty complex to model and research

A good rule of thumb is to design the injector to have a pressure drop about equal to 20% of the chamber pressure Using this formula

Where Cd is the discharge coefficient, a nondimensional number that measures ‘how much flow gets through an orifice’ and can be estimated by the shape of the orifice
In general, a larger number of smaller holes gives better mixing, atomization, and combustion efficiency
But we don’t use this philosophy much because someone is gonna have to machine those tiny holes, and you’ll wish it isn’t you There may also be worry of combustion instabilities as the number of orifices increases
Knowing the entry angle of propellants into the chamber can give you a good estimate of the resultant angle after impingement This is critical because we want the fluids going axially down the chamber towards the nozzle exit, not combusting onto the chamber walls
But some designs require more sophisticated empirical approximations
The manifold is the space right before the orifices that makes sure the propellants are distributed evenly across the injector
The shape and volume of the manifolds are designed for desirable flow behavior
Usually (but not always), we prefer to ox-center, meaning the (usually lower temperature) oxidizer is the central propellant – so uncombusted oxidizer will land on the chamber wall and act as a coolant
Rocket combustion always results in random chamber pressure fluctuations
When these fluctuations get out of control, it’s called combustion instability, and it’s very very bad
The injector can be designed to help mitigate these instabilities

Return to Learning Curriculum

No labels

13 of 14 | 9/18/2024, 1:19 PM

14 of 14 | 9/18/2024, 1:19 PM

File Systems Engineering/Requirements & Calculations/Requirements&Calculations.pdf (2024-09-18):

# Requirements and Calculations of a Liquid Rocket Engine

### Will Armentrout

### September 15, 2024

## Contents

1 Nomenclature and Terms | 1
2 System Requirements/Specifications | 2
3 Derivations, Formulas & Calculation Process | 3
4 Design Equations | 6

## 1 Nomenclature and Terms

N2O - Nitrous Oxide
IP A - Isopropyl Alcohol
Isp - Specific Impulse
O/F - Oxidizer/Fuel Ratio

## 2 System Requirements/Specifications

Requirement | Value | From?
Thrust | 900 N | Rocket Weight
Specific Impulse | 226 s | NASA CEA
Tank Pressure | 5.127 MPa | Property (Vapor Pressure: 20 C)
O/F Mole Ratio | 9 | Ideal Reaction
O/F Mass Ratio | 6.6 | Calculated (O/F Mole Ratio)
Weight Flow Rate | 3.6 N/s | Calculated (Thrust and Isp)
Mass Flow Rate | 0.4059 kg/s | Calculated (Weight Flow Rate)
Ox Mass Flow Rate | 0.3525 kg/s | Calculated (Mass Flow Rate)
Fuel Mass Flow Rate | 0.0534 kg/s | Calculated (Mass Flow Rate)
Chamber Pressure | 3 MPa | Assumed (Tank Pressure)
Chamber Temperature | 2966 K | NASA CEA
Chamber Gas Density | 3.3349 kg/m3 | NASA CEA
Chamber Gamma | 1.1459 | NASA CEA
Chamber Mach Number | 0.00 | Assumption
Chamber SoS | 1015 m/s | NASA CEA
Throat Pressure | 1.7248 MPa | NASA CEA
Throat Temperature | 2790 K | NASA CEA
Throat Gas Density | 2.0577 kg/m3 | NASA CEA
Throat Gamma | 1.1471 | NASA CEA
Throat Mach Number | 1.00 | Definition
Throat SoS | 981 m/s | NASA CEA
Exit Pressure | 0.1 MPa | Estimated (Altitude)
Exit Temperature | 1907 K | NASA CEA
Exit Gas Density | 0.17948 kg/m3 | NASA CEA
Exit Gamma | 1.2044 | NASA CEA
Exit Mach Number | 2.708 | NASA CEA
Exit SoS | 819 m/s | NASA CEA
Area Ratio | 5.0683 | NASA CEA
C* | 1487 m/s | NASA CEA
Specific Gas Constant | 32.4638 g/mol | NASA CEA
Throat Area | 65.591mm² | Calculated (Isentropic Equations)
Throat Diameter | 9.1385 mm | Calculated
Exit Area | 332.4343mm² | Calculated (Area Ratio)
Exit Diameter | 20.5734 mm | Calculated
Nozzle Exit Angle | 15◦ | Determined (Hobby Rocket Engines)
Throat Entry Angle | 30◦ | Determined (Youngblood)
Characteristic Length | 1 m | Determined (Youngblood)
Chamber Diameter | 30 mm | Determined
Chamber Length | 84.36 mm | Calculated (Hobby Rocket Engines)
Chamber Wall Thickness | 5 mm | Calculated & Determined

## 3 Derivations, Formulas & Calculation Process

### 3.1 Deriving Oxidizer/Fuel Ratio

Ideal Reaction: C3H8O + 9N2O → 3CO2 + 4H2O + 9N2

In reality the reaction is more complicated. the heat of reaction causes many radicals and exotic species that can be calculated but are ignored for simplicity.

Mole O/F Ratio of 9 (9 Moles of N2O for 1 mole of C3H8O).
MN2O = 2 ∗ 14 + 16 = 44, MC3H8O = 3 ∗ 12 + 8 ∗ 1 + 16 = 60

O/FMass =

9∗44
60 = 6.6 (6.6 kg of N2O for 1 kg of C3H8O)

### 3.2 NASA CEA

Once these variables have been determined the NASA CEA (Chemical Equalibrium with Applications) or other equalibrium solver can be used to get many other critical parameters.

### 3.2.1 Procedure for running the NASA CEA

This is by no means the only way to do it. This is also intended as an early design exercise where other chamber pressures and O/F ratios should be analyzed. If you just want a single analysis point don’t use the interval tabs and just use the number entry on the right side of the tabs for pressure and O/F ratio.

1. Look up NASA CEA on any browser. URL: https://cearun.grc.nasa.gov/
2. On the right hand side in the chemical equalibrium problem types check ”Rocket”. Then hit submit.
3. On the ”Pressure” tab (should be autoselected) enter values for the chamber pressure.

This will be based on the tank pressure (5.127 MPa) and the losses in the plumbing to the chamber.

Since MPa, isn’t a selectable option, multiply the MPa number by 10 to get the pressure in bar.

Assume 3 MPa as an approximate starting point. Since 3 MPa is our goal pressure, input 2 MPa (20 bar) as a Low Value and 5 MPa (50 bar) as a high value.

Make the interval smaller, maybe 0.5 MPa (5 bar) to see a range of pressure values.

Accept Input and Continue.

4. On the ”Fuel(s)” tab check the ”Use Periodic Table (mixtures)” since IPA isn’t on the quick select list. Accept Fuel Selection and Continue.
5. On the ”Periodic Table” check Hydrogen, Carbon and Oxygen (as these are the component elements in IPA). Accept Element Selections and Continue.

6. On the ”Select your Fuel(s)” tab check C3H8O, 2propanol (This is the chemical formula and name for Isopropyl Alcohol). Accept Selected Reactant(s) and Continue. There should be a confirmation form, Fuel Mix form and Component Properties form. Accept inputs for all and continue to the next form.
7. On the ”Select your Oxidizer(s)” tab check N2O. Accept Oxidizer Selection and Continue to the next form.
8. On the ”Enter proportions of Oxidizer/Fuel” on the top selection area select Specify with Oxidizer/Fuel Wt. Ratio.
| We calculated the stoichometric O/F weight ratio earlier as being 6.6.
| If 6.6 is the target value enter a low value of 4 and a high value of 8 and use an interval of 0.2.
9. On the ”Define Exit Conditions” tab define Chamber/Exit Pressure Ratios on the left hand side.
| In rocket engines the most efficient engine is one that is perfectly expanded (mean- ing the pressure at the exit of the nozzle is at ambient pressures).
| A rocket engine will fly in a multitude of different pressures as it travels upward (pressure decreases with altitude), but for now we will analyze with a exit pressure of 1 bar (or about 110m in altitude) as a baseline.
| In order to get an exit pressure of 1 bar we take our chamber pressure range (2-5 MPa in steps of 0.5 MPa or 20-50 bar in steps of 5 bar) and divide it by the desired exit pressure.
| So for this it’s easy. The ratios are just the chamber pressure values. You will have to input each ratio manually (20, 25, 30 ... to 50) on the left column.
| Accept Input and Continue to Next Form.
10. On the ”Enter Your Final Choices Before Running CEA” the autogenerated selections should be good (Short, Mass-Fractions, Equilibrium). You can look at your entered ranges for chamber pressure, O/F ratio and chamber/exit pressure ratios before you run the CEA. Submit Input and Perform CEA Analysis.
11. The CEA should run in less than a couple of seconds. The file displayed in the embedded window is the output file. You can download the input and output files in the top right.

### 3.2.2 Procedure for analyzing the NASA CEA output

The output file of the NASA contains many valuable pieces of information that will be useful in designing a rocket engine later. A navigation tip: the CEA output file is sorted from smallest to largest O/F ratio first and within each O/F ratio it is sorted by chamber pressure.

1. Scroll through the output file to find the O/F Ratio of 6.6 and the Pin of 3 MPa (435.1 psi). For some reason the CEA output only displays the chamber pressures in psi no matter the input unit.

2. Once you have found the section where Pin = 435.1 psi and O/F = 6.6 find the exit condition where the P, bar equals 1.000 or Pinf/P = 30.

The chamber, throat and exit pressure column where P, BAR = 1.000 (or another exit pressure) are the only columns of interest per section.

3. Find and record the variables of interest. In our case this would be pressure (P), temperature (T), density (RHO), mach number, specific heat ratio (GAMMA), speed of sound (SON VEL), area ratio (Ae/At), c star, specific impulse (Isp) and the mass fractions. Here are the values:
| Pressure at the throat: 17.248 Bar
| Temperature in the combustion chamber: 2966 K, throat: 2790 K, exit: 1907 K
| Density of the combustion gases in the combustion chamber: 3.3349 kg/m3, throat 2.0577 kg/m3, exit 0.17948 kg/m3
| Mach Number at exit: 2.708
| Specific Heat Ratio at the combustion chamber: 1.1459, throat: 1.1471, exit:
| 1.2044
| Speed of Sound at the combustion chamber: 1015 m/s, throat: 981 m/s, exit: 819 m/s
| Area Ratio: 5.0683
| C star: 1487 m/s
| Specific Impulse: 2218 m/s. In order to convert this to the familiar specific impulse with units of seconds divide by the gravitational constant g = 9.81. Isp =
| 2218 9.81 = 226s
| The mass fractions are listed for the main combustion gas products.
| – CO: Combustion Chamber - 0.05069, Throat - 0.03951, Exit - 0.00258 – CO2: Combustion Chamber - 0.20943, Throat - 0.22700, Exit - 0.28503 – H: Combustion Chamber - 0.00010, Throat - 0.00007, Exit - 0.00000 – HO2: Combustion Chamber - 0.00003, Throat - 0.00002, Exit - 0.00000 – H2: Combustion Chamber - 0.00083, Throat - 0.00065, Exit - 0.00006 – H2O: Combustion Chamber - 0.14328, Throat - 0.14690, Exit - 0.15703 – NO: Combustion Chamber - 0.01266, Throat - 0.00909, Exit - 0.00047 – NO2: Combustion Chamber - 0.00002, Throat - 0.00001, Exit - 0.00000 – N2: Combustion Chamber - 0.54681, Throat - 0.54849, Exit - 0.55252 – O: Combustion Chamber - 0.00151, Throat - 0.00093, Exit - 0.00001 – OH: Combustion Chamber - 0.01160, Throat - 0.00850, Exit - 0.00041 – O2: Combustion Chamber - 0.02302, Throat - 0.01885, Exit - 0.00190

### 3.3 Deriving the Flow rates

Specific Impulse Equation: Isp =

| T

mg˙ 0 → Weight Flow Version: W˙ = ˙mg0 =
T
Isp
Solve: W˙ =
900N
226s = 3.982N/s

Convert to mass flow: ˙m =

W˙
g0 → m˙ =

3.9823
9.81 = 0.4059kg/s

Separate into oxidizer and fuel mass flow rates: Oxidizer - Nitrous Oxide: ˙mN2O = ˙m ∗

6.6
7.6 = 0.3525kg/s
Fuel - Isopropyl Alcohol: ˙mIP A = ˙m ∗

1
7.6 = 0.0534kg/s

## 4 Design Equations

### 4.1 Nozzle Design Equations

### 4.1.1 Solving for the specific gas constant

The Univeral Gas Constant R¯ is 8.314 J/molK. The specific gas constant is R =

R¯
M where M is the molecular weight of the mixture of product gases. Need to solve for the molecular weight of all of the component gases and their moles in mass fraction.
| CO: M = 12 + 16 = 28 xCO = 28 · 0.03951 = 1.1063 moles
| CO2: M = 12 + 16 + 16 = 44 xCO2 = 44 · 0.2270 = 9.988 moles
| H: M = 1 xH = 1 · 0.00007 = 0.00007 moles
| HO2: M = 1 + 16 + 16 = 33 xHO2 = 33 · 0.00002 = 0.00066 moles
| H2: M = 1 + 1 = 2 xH2 = 2 · 0.00065 = 0.0013 moles
| H2O: M = 1 + 1 + 16 = 18 xH2O = 18 · 0.1469 = 2.6442 moles
| NO: M = 14 + 16 = 30 xNO = 30 · 0.00909 = 0.2727 moles
| NO2: M = 14 + 16 + 16 = 46 xNO2 = 46 · 0.00001 = 0.00046 moles
| N2: M = 14 + 14 = 28 xN2 = 28 · 0.54849 = 15.3577 moles
| O: M = 16 xO = 16 · 0.00093 = 0.01488 moles
| OH: M = 16 + 1 = 17 xOH = 17 · 0.0085 = 0.1445 moles
| O2: M = 16 + 16 = 32 xO2 = 32 · 0.01885 = 0.6032 moles
| Total: xtotal = 1.1063+9.988+0.00007+0.00066+0.0013+2.6442+0.2727+0.00046+
15.3577 + 0.01488 + 0.1445 + 0.6032 = 30.1346 moles

Molecular weight of mixture is M = 28·

1.1063
30.1346 +44·

9.988
30.1346 +1·

0.00007
30.1346 +33·

0.00066
30.1346 +2·

0.0013
30.1346 +
18·

2.6442
30.1346+30·

0.2727
30.1346+46·

0.00046
30.1346+28·

15.3577
30.1346+16·

0.01488
30.1346+17·

0.1445
30.1346+32·

0.6032
30.1346 = 32.4645g/mol

Solve for specific gas constant R =

8.314
32.4645 = 0.2561J/gK = 256.1J/kgK

### 4.1.2 Throat Area

Mass Flow Rate at the throat: ˙m = At √

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
2(1−γ)

Area of Throat: At =

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
2(γ−1)

Values used in the Equation:
Mass Flow Rate ˙m = 0.4059kg/s
Stagnation Temperature To = Tchamber = 2966K Stagnation Pressure Po = Pchamber = 3MP a
Gamma (at the throat) γthroat = 1.1471
Specific Gas Constant (at the throat) Rthroat = 256.1J/kgK

Plug in the numbers: At =

0.4059·

√
2966
3·10⁶

q 256.1
1.1471 (

1.1471+1
2

)

1.1471+1
2(1.1471−1) = 6.5591 · 10⁻⁵m²

Solve for Diameter At = π

Dt

2
4 → Dt =

q4At
π =

q4·(6.5591·10⁻⁵)
π = 0.0091385m = 9.1385mm

### 4.1.3 Exit Area

Use the throat area and determined Ae/At to get the exit area. Ae
At

= 5.0683
Ae = 5.0683 · 6.5591 · 10⁻⁵ = 3.3243 · 10⁻⁴m²

Diameter: De =

q4Ae
π =

q4·(3.3243·10⁻⁴)
π = 0.02057m = 20.5734mm

### 4.1.4 Nozzle Angles

In normal commercial rocket engines the nozzle angle is optimized so that when the flow leaves it is as 1D as possible, to achieve max thrust. The profile that maximizes thrust for a certain throat area and length is called an ”Rao optimum contour”. This is is named after G.V.R Rao and is complicated to manufacture. Because of its complexity we will just use a 15◦
conical nozzle profile, common for hobby and small area ratio engines. It has 98.3% of the performance of an ideal nozzle, so close enough for me.

### 4.2 Combustion Chamber Equations

### 4.2.1 Chamber Length

For the combustion chamber Hobby Rocket Engines references a combustion chamber with a cross sectional area of at least 3 times the throat area. For this reason we choose a chamber diameter of 30 mm, much larger than the required size, subject to change based on the injector.

The chamber volume required for complete combustion is defined by the characteristic chamber length: L

∗ = Vc/At → L

∗At = Vc where Vc = AcLc+ convergent volume Youngblood references a characterisitc length of 1m being successful in nitrous, ethanol engines so that value will be used as a minimum.

For small combustion chambers the convergent volume is 1/10th the cylindrical portion so Vc = 1.1AcLc
Combine Equations L

∗At = 1.1AcLc → Lc =

L∗At
1.1Ac

=

(1)(6.5591·10⁻⁵
)
1.1(π

0.032
)

= 0.08436m or 84.36mm

### 4.2.2 Chamber Thickness

This system will definitely not be thin walled but it is a good starting point for minimums. The axial or longnitudinal stress in a thin walled pressure vessel is given by the equation: σa =

P r
2t Where P is the pressure, r is radius and t is the thickness.

Rrearrange for thickness: t =

P r
2σa

In our case pressure is the chamber pressure (3 MPa), radius is 15 mm and sigma is material dependent. Since steel is cheap we will use that, heat transfer be damned (hopefully we don’t run it for long enough). Steel rod stock on McMaster has a tensile yield stress of 60,000 psi or 413.685 MPa.
Plug this in: t =

3·15
2·413.685 = 0.054389mm Remember this number is at ambient temperatures and the combustion chamber gas were calculated to be at 2966 K (Above the melting point of steel).

Recalculating with an operating temperature of 500◦C or 773.15 K steel has about 40% of it’s yield strength at 21C. Using this: t =

3·15
2·(0.4)(413.685)· = 0.13597mm
Not really much of a worry, but let’s use something thick enough to handle the heat loads as well, call the wall thickness 5mm.

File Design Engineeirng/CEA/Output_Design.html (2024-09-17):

         NASA-GLENN CHEMICAL EQUILIBRIUM PROGRAM CEA2, FEBRUARY 5, 2004
                   BY  BONNIE MCBRIDE AND SANFORD GORDON
      REFS: NASA RP-1311, PART I, 1994 AND NASA RP-1311, PART II, 1996

 *******************************************************************************

 ### CEA analysis performed on Mon 16-Sep-2024 23:36:59
  
 # Problem Type: "Rocket" (Infinite Area Combustor)
  
 prob case=_______________3309 ro equilibrium
  
 # Pressure (1 value):
 p,bar= 30
 # Chamber/Exit Pressure Ratio (1 value):
 pi/p= 30
  
 # Oxidizer/Fuel Wt. ratio (1 value):
 o/f= 6.6
  
 # You selected the following fuels and oxidizers:
 reac
 fuel C3H8O,2propanol   wt%=100.0000
 oxid N2O               wt%=100.0000
  
 # You selected these options for output:
 # short version of output
 output short
 # Proportions of any products will be expressed as Mass Fractions.
 output massf
 # Heat will be expressed as siunits
 output siunits
  
 # Input prepared by this script:/var/www/sites/cearun.grc.nasa.gov/cgi-bin/CEARU
 N/prepareInputFile.cgi
  
 ### IMPORTANT:  The following line is the end of your CEA input file!
 end

              THEORETICAL ROCKET PERFORMANCE ASSUMING EQUILIBRIUM

           COMPOSITION DURING EXPANSION FROM INFINITE AREA COMBUSTOR

 Pin =   435.1 PSIA
 CASE = _______________

             REACTANT                    WT FRACTION      ENERGY      TEMP
                                          (SEE NOTE)     KJ/KG-MOL      K  
 FUEL        C3H8O,2propanol              1.0000000         0.000      0.000
 OXIDANT     N2O                          1.0000000         0.000      0.000

 O/F=    6.60000  %FUEL= 13.157895  R,EQ.RATIO= 0.998838  PHI,EQ.RATIO= 0.998709

                 CHAMBER   THROAT     EXIT
 Pinf/P            1.0000   1.7393   30.000
 P, BAR            30.000   17.248   1.0000
 T, K             2966.32  2789.71  1907.06
 RHO, KG/CU M    3.3349 0 2.0577 0 1.7948-1
 H, KJ/KG         0.00000  -480.75 -2459.83
 U, KJ/KG         -899.58 -1318.99 -3016.99
 G, KJ/KG        -28371.3 -27162.8 -20699.8
 S, KJ/(KG)(K)     9.5645   9.5645   9.5645

 M, (1/n)          27.417   27.671   28.459
 (dLV/dLP)t      -1.01202 -1.00939 -1.00067
 (dLV/dLT)p        1.2692   1.2246   1.0236
 Cp, KJ/(KG)(K)    3.5066   3.2745   1.7962
 GAMMAs            1.1459   1.1471   1.2044
 SON VEL,M/SEC     1015.3    980.6    819.2
 MACH NUMBER        0.000    1.000    2.708

 PERFORMANCE PARAMETERS

 Ae/At                      1.0000   5.0683
 CSTAR, M/SEC               1486.9   1486.9
 CF                         0.6595   1.4918
 Ivac, M/SEC                1835.4   2469.2
 Isp, M/SEC                  980.6   2218.0

 MASS FRACTIONS

 *CO              0.05069  0.03951  0.00258
 *CO2             0.20943  0.22700  0.28503
 *H               0.00010  0.00007  0.00000
 HO2              0.00003  0.00002  0.00000
 *H2              0.00083  0.00065  0.00006
 H2O              0.14328  0.14690  0.15703
 *NO              0.01266  0.00909  0.00047
 NO2              0.00002  0.00001  0.00000
 *N2              0.54681  0.54849  0.55252
 *O               0.00151  0.00093  0.00001
 *OH              0.01160  0.00850  0.00041
 *O2              0.02302  0.01885  0.00190

  * THERMODYNAMIC PROPERTIES FITTED TO 20000.K

 NOTE. WEIGHT FRACTION OF FUEL IN TOTAL FUELS AND OF OXIDANT IN TOTAL OXIDANTS

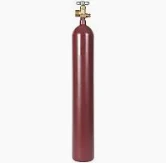
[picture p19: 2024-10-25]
Design Engineeirng/Plumbing/Nitrous Tank.webp

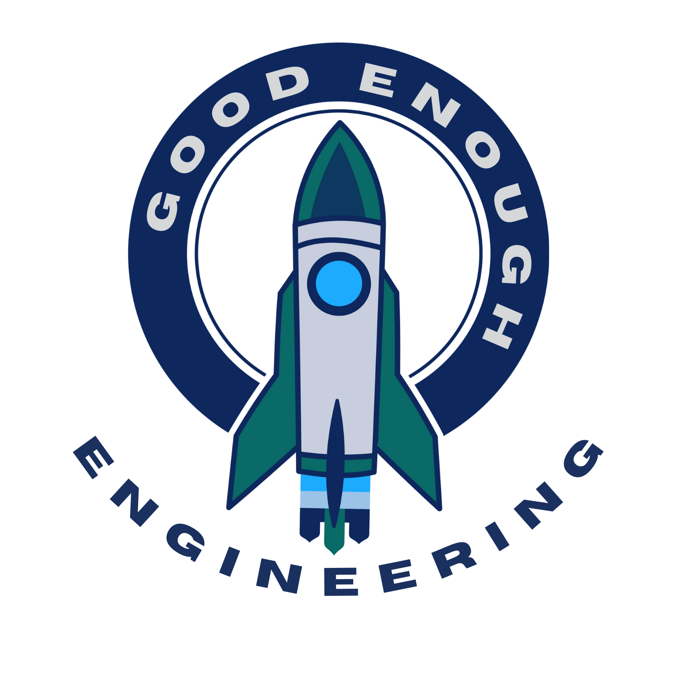
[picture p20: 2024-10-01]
YT/Woodies_Transparent_2.png

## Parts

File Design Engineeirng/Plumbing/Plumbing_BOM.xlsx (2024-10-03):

Plumbing Possible Solutions |  |  |  |  |  |  |  |  |  | Nitrous Oxide Properties |  |  |  | IPA Properties
Pressure Vessels |  |  |  |  |  |  |  |  |  | Phase | Pressure (MPa) | Temperature (K) | Density (kg/m^3) | Phase | Pressure (MPa) | Temperature (K) | Density (kg/m^3)
Name | Component | Pressure Rating (psi) | ID (in) | Length (in) | Volume (m^3) | Capacity (kg) | Material | Pipe Size | Price | Liquid | 5.0525 | 293.15 | 785.1 | Liquid | ? | 293.15 | 786
PV-2514SW (https://hydrocomponents.us/collections/hcti-housing-pressure-vessels/products/pv-2514sw-1000-psi-frp-fiberglass-membrane-housing-free-seawater-membrane-includ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) | Pressure Vessel | 1000 | 2.5 | 14 | 0.001126152974 | 0.8841426999 | Fiberglass | 1/4" FNPT | 455 | Vapor | 5.0525 | 293.15 | 157.99
PV-2521SW (https://hydrocomponents.us/collections/hcti-housing-pressure-vessels/products/pv-2521sw-1000-psi-frp-fiberglass-membrane-housing-free-seawater-membrane-includ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) | Pressure Vessel | 1000 | 2.5 | 21 | 0.001689229461 | 1.32621405 | Fiberglass | 1/4" FNPT | 395
PV-2540SW (https://hydrocomponents.us/collections/hcti-housing-pressure-vessels/products/pv-2540sw-1000-psi-frp-fiberglass-membrane-housing-free-seawater-membrane-includ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) | Pressure Vessel | 1000 | 2.5 | 40 | 0.003217579926 | 2.526122 | Fiberglass | 1/4" FNPT | 525
WAV-PV-2540-FRP-1000-EP (https://pwnps.com/products/membrane-pressure-vessel-2-5-x-40-1000-psi-rating-end-port-design-wave-cyber) | Pressure Vessel | 1000 | 2.5 | 40 | 0.003217579926 | 2.526122 | Fiberglass | 1/4" FNPT | 690
NP-PV-2521-1000 (https://www.lenntech.com/products/Lenntech-PV/NP-PV2540-1000/2540-2,5-1000-psi-Pressure-Vessel/index.html) | Pressure Vessel | 1000 | 2.5 | 21 | 0.001689229461 | 1.32621405 | ANSI 316L (SS) | 1/4" FNPT | ?
NP-PV-2540-1000 (https://www.lenntech.com/products/Lenntech-PV/NP-PV2540-1000/2540-2,5-1000-psi-Pressure-Vessel/index.html) | Pressure Vessel | 1000 | 2.5 | 40 | 0.003217579926 | 2.526122 | ANSI 316L (SS) | 1/4" FNPT | ?
L27DV Faber Cylinder (https://www.piranhadivemfg.com/item/L27DV-Faber-Cylinder-w-No-Valve-BLACKFree-Domestic-Ground-Shipping--13910) | Pressure Vessel (N2O) | 2640 | 5.46 | 14.43 | 0.004 | 3.1404 | Aluminum? SS? |  | 240
22 CUFT Aluminum Oxygen Cylinder (https://gascylindersource.com/shop/oxygen-cylinders/22-cu-ft-aluminum-oxygen-cylinder/) | Pressure Vessel (N2O) | 1800 | 5.25 | 17.1 | 0.004 | 3.1404 | Aluminum | 0.750 UNF | 119.4
2.5 LB Aluminum CO2 Cylinder (https://gascylindersource.com/shop/co2-carbon-dioxide-cylinders/2-5-lb-aluminum-co2-cylinder-new/) | Pressure Vessel (IPA) | 1800 | 4.4 | 10.4 | 0.0016 | 1.2576 | Aluminum | 0.750 UNF | 47.6
Pressure Sensors
Name | Component | Pressure Range (psi) | Fluid Interface | Electrical Interface | Accuracy | Material | Price
0-1000 PSI High Accuracy Pressure Transducers (https://www.dataq.com/products/accessories/pressure-sensor/2000361-hs-1000.html) | Pressure Transducer | 0-1000 | 1/4"-18 or 1/8"-27 NPT | 0.5-4.5V Linear Output for 4-20mA | 0.50% | 316 SS | $68
0-1500 PSI High Accuracy Pressure Transducers (https://www.dataq.com/products/accessories/pressure-sensor/2000361-hs-1500.html) | Pressure Transducer | 0-1500 | 1/4"-18 or 1/8"-27 NPT | 0.5-4.5V Linear Output for 4-20mA | 0.50% | 316 SS | $68
High Precision Stainless Pressure Transducer (https://www.amazon.com/Precision-Stainless-Pressure-Transducer-Sensor/dp/B0D236XDHP?th=1) | Pressure Transducer | 0-1000 | G 1/4" | 0.5-4.5V Linear Output | 0.50% | SS | $15.13
1000 PSI Pressure Transducer Sensor (https://www.amazon.com/FUSCH-Transducer-Connector-Stainless-Transmitter/dp/B0CRQT7VFJ?s=industrial) | Pressure Transducer | 0-1000 | 1/8"-27 NPT | 0.5-4.5V Linear Output | 1.00% | 304 SS | $32.69
Low Cost IOT Small Pressure Sensor (https://www.alibaba.com/product-detail/Low-Cost-IOT-Small-Pressure-Sensor_60747890200.html) | Pressure Transducer | 0-15 MPa | G1/4, M12*1.5, 1/4NPT, 7/16-20UNF female | 12C, SPI, 0.2-2.9V | 0.5, 1, 2% |  | $10

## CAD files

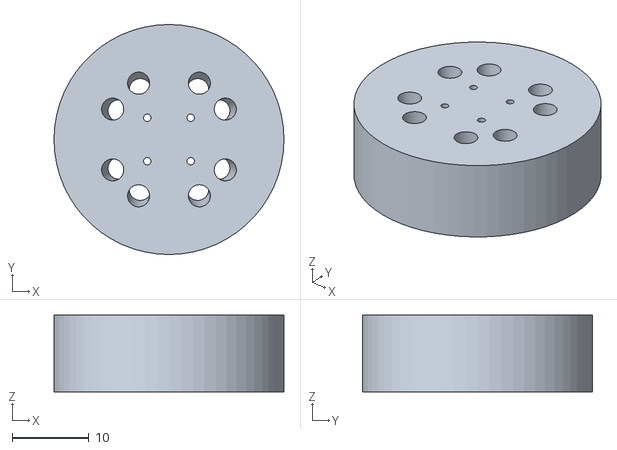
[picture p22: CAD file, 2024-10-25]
Design Engineeirng/CAD/Engine_Assembly - InjectorPlate-1.STL
30.0 x 30.0 x 10.0

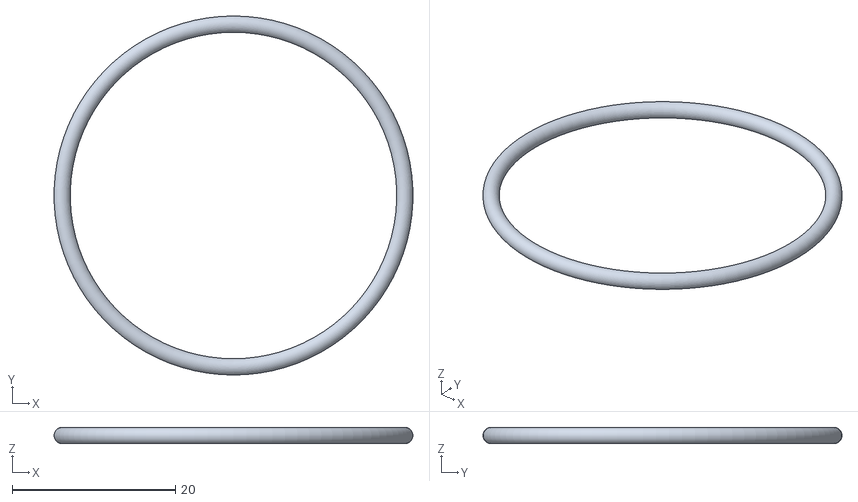
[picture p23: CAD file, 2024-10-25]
Design Engineeirng/CAD/Engine_Assembly - O-ring_2x40mm-3.STL
44.0 x 44.0 x 2.00

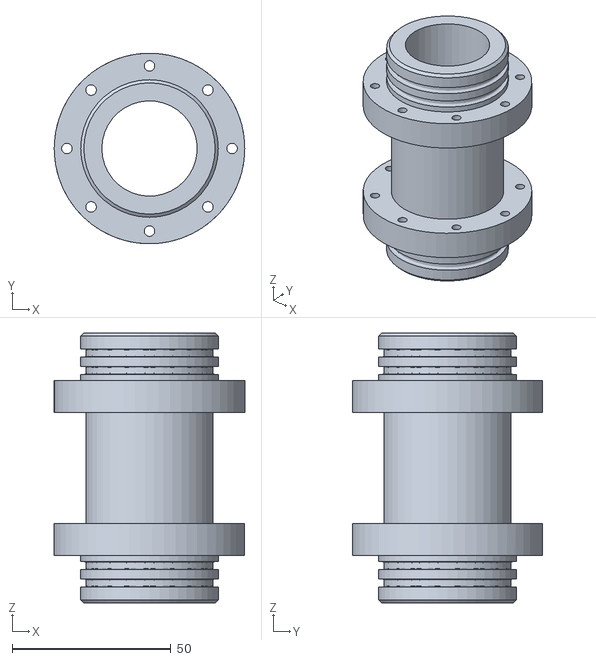
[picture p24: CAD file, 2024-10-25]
Design Engineeirng/CAD/Engine_Assembly - Combustion_Chamber-2.STL
60.0 x 60.0 x 85.0

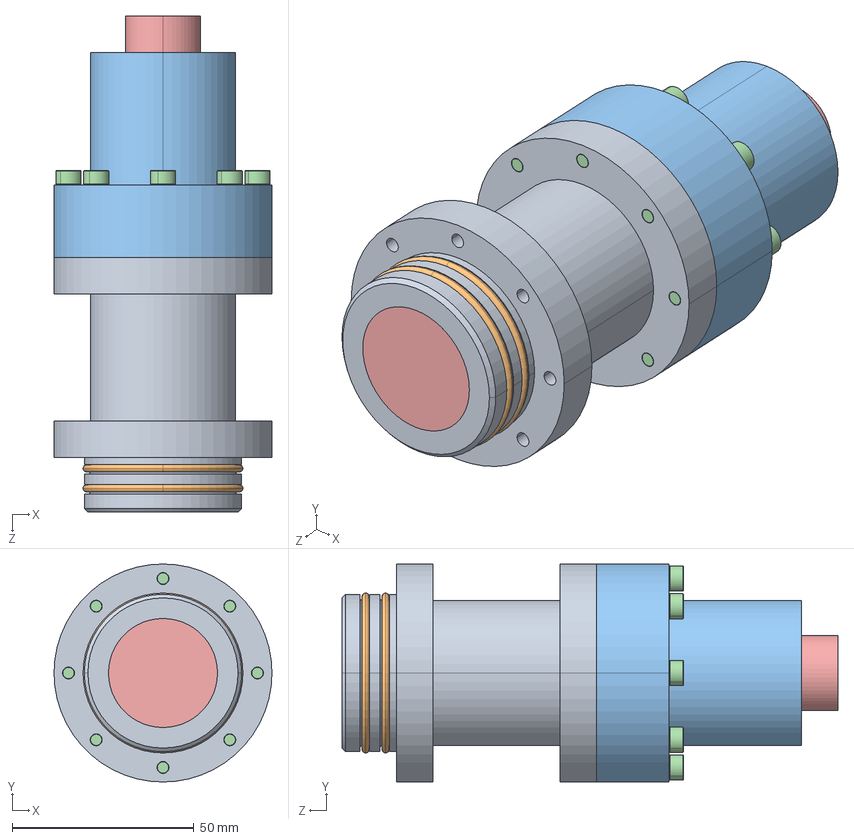
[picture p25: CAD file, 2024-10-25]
Design Engineeirng/CAD/Engine_Assembly.STEP
60.0 x 60.0 x 136.5 mm
Combustion_Chamber
O-ring_2x40mm x 4
Nozzle
91290A180_Alloy Steel Socket Head Screw_91290A180 x 8
Fluid_Volume
InjectorPlate

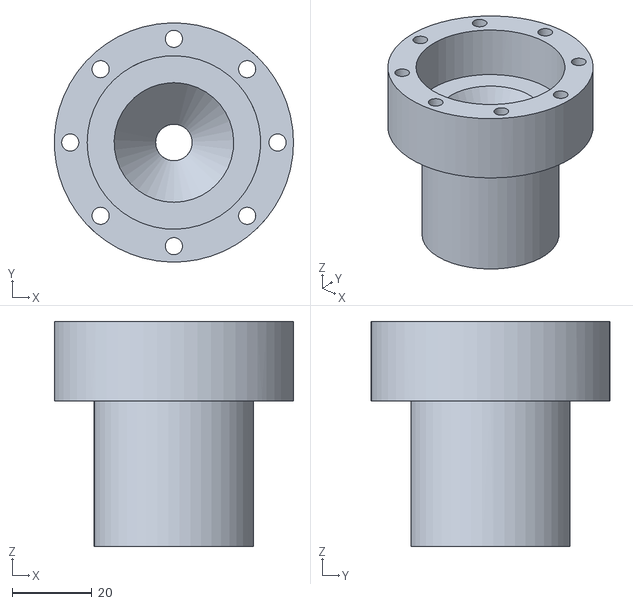
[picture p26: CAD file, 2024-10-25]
Design Engineeirng/CAD/Engine_Assembly - Nozzle-1.STL
60.0 x 60.0 x 56.5

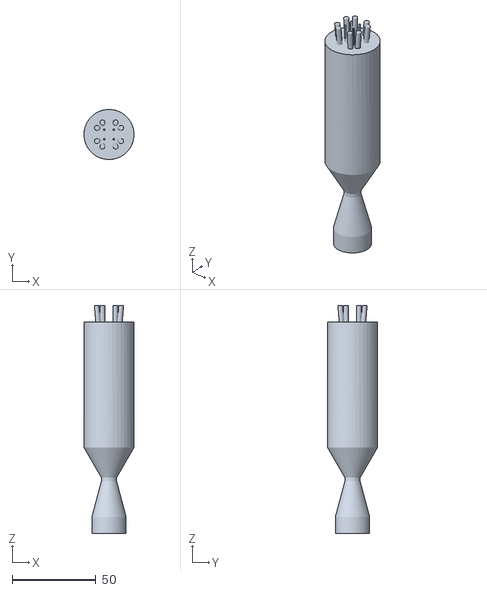
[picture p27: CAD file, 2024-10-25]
Design Engineeirng/Injector/Fluid_Volume.STL
30.0 x 30.0 x 136.5

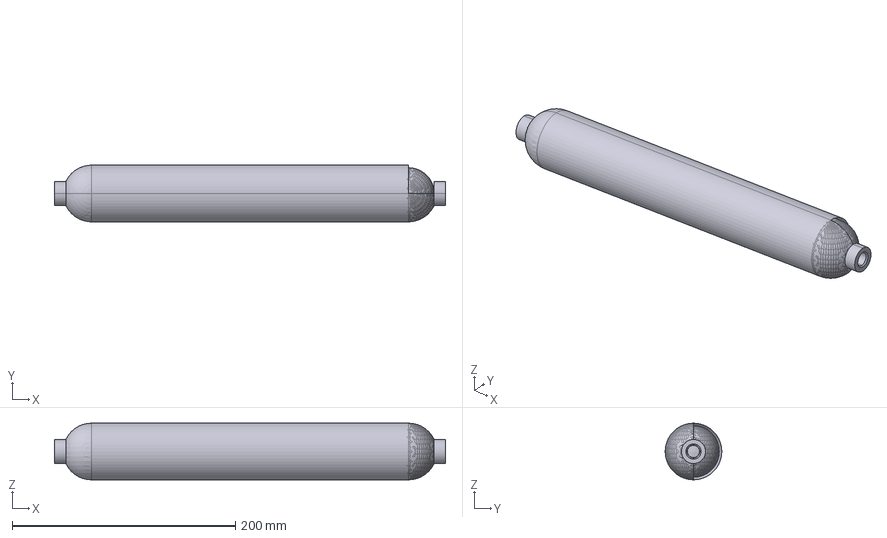
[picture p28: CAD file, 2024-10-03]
Design Engineeirng/Plumbing/316L-HDF4-500-SwagelokCompany-3D-09-30-2024.stp
350.5 x 50.8 x 50.8 mm

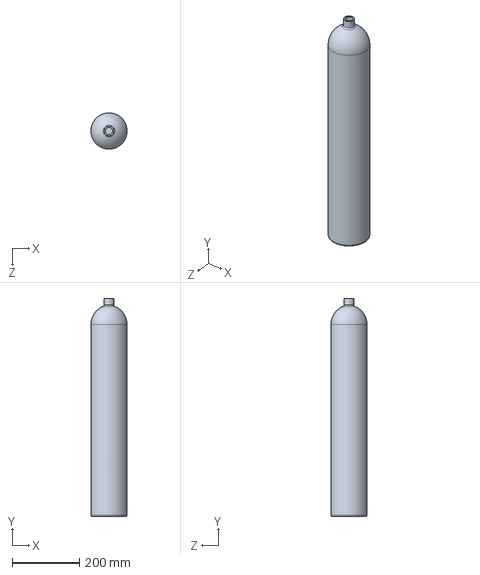
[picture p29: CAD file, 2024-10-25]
Design Engineeirng/CAD/N2O_Tank.SLDPRT
107.9 x 649.3 x 108.0 mm

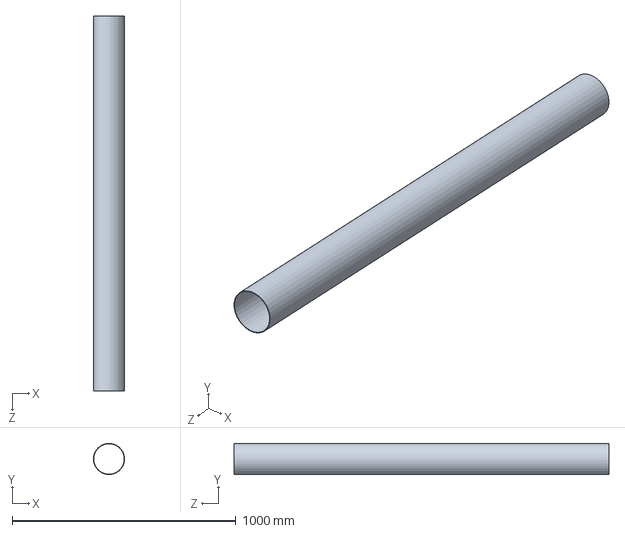
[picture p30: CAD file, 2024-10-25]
Design Engineeirng/CAD/Rocket_Shell.SLDPRT
139.7 x 139.5 x 1676.4 mm

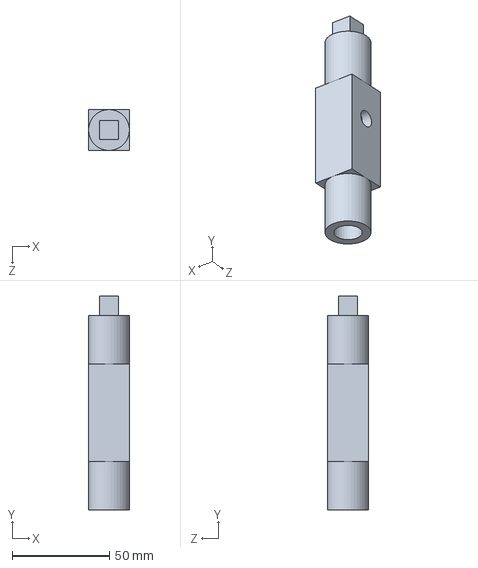
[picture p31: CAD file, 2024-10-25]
Design Engineeirng/CAD/N2O_Tank_Valve.SLDPRT
21.0 x 110.0 x 21.0 mm

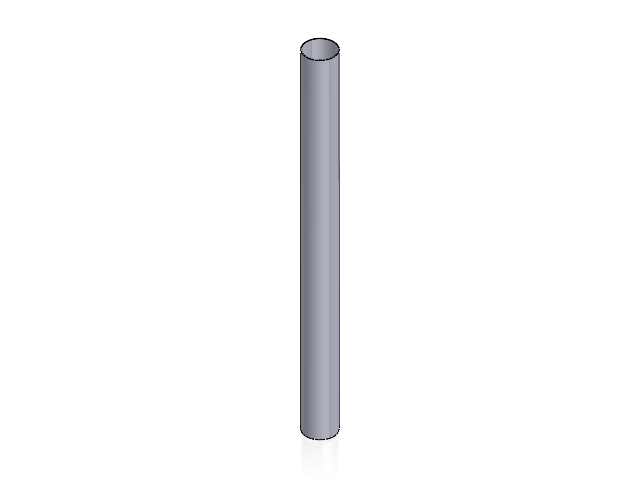
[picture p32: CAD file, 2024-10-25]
Design Engineeirng/CAD/Rocket.SLDASM
Rocket_Shell
N2O_Tank
Combustion_Chamber
O-ring_2x40mm x 4
Nozzle
91290A180_Alloy Steel Socket Head Screw x 8
N2O_Tank_Valve

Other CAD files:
Design Engineeirng/CAD/Engine_Assembly - O-ring_2x40mm-1.STL
Design Engineeirng/CAD/Engine_Assembly - O-ring_2x40mm-4.STL
Design Engineeirng/CAD/Engine_Assembly - O-ring_2x40mm-2.STL
Design Engineeirng/Injector/InjectorPlate.SLDPRT
Design Engineeirng/CAD/Fluid_Volume.STEP
Design Engineeirng/CAD/Combustion_Chamber.SLDPRT
Design Engineeirng/CAD/O-ring_2x40mm.SLDPRT
Design Engineeirng/CAD/91290A180_Alloy Steel Socket Head Screw.SLDPRT
Design Engineeirng/CAD/Engine_Assembly - 91290A180_Alloy Steel Socket Head Screw-1.STL
Design Engineeirng/CAD/Engine_Assembly - 91290A180_Alloy Steel Socket Head Screw-2.STL
Design Engineeirng/CAD/Engine_Assembly - 91290A180_Alloy Steel Socket Head Screw-3.STL
Design Engineeirng/CAD/Engine_Assembly - 91290A180_Alloy Steel Socket Head Screw-4.STL
Design Engineeirng/CAD/Engine_Assembly - 91290A180_Alloy Steel Socket Head Screw-5.STL
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

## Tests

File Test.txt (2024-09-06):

git add *
git commit -m "message"
git push origin some branch name perhaps

%to pull from cloud
git pull origin

%to switch branches
git checkout branch name

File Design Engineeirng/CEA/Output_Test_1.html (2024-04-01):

         NASA-GLENN CHEMICAL EQUILIBRIUM PROGRAM CEA2, FEBRUARY 5, 2004
                   BY  BONNIE MCBRIDE AND SANFORD GORDON
      REFS: NASA RP-1311, PART I, 1994 AND NASA RP-1311, PART II, 1996

 *******************************************************************************

 ### CEA analysis performed on Wed 13-Mar-2024 21:08:24
  
 # Problem Type: "Rocket" (Infinite Area Combustor)
  
 prob case=Test___________9648 ro equilibrium
  
 # Pressure (15 values):
 p,atm= 1, 2, 3, 4, 5, 6, 7, 8, 9, 10, 11, 12, 13, 14, 15
 # Chamber/Exit Pressure Ratio (6 values):
 pi/p= 1, 5, 10, 15, 20, 25
  
 # Oxidizer/Fuel Wt. ratio (9 values):
 o/f= 3, 3.5, 4, 4.5, 5, 5.5, 6, 6.5, 7
  
 # You selected the following fuels and oxidizers:
 reac
 fuel C3H8O,2propanol   wt%=100.0000  t,k= 298.150
 oxid N2O               wt%=100.0000  t,k= 298.150
  
 # You selected these options for output:
 # short version of output
 output short
 # Proportions of any products will be expressed as Mass Fractions.
 output massf
 # Heat will be expressed as siunits
 output siunits
  
 # Input prepared by this script:/var/www/sites/cearun.grc.nasa.gov/cgi-bin/CEARU
 N/prepareInputFile.cgi
  
 ### IMPORTANT:  The following line is the end of your CEA input file!
 end

              THEORETICAL ROCKET PERFORMANCE ASSUMING EQUILIBRIUM

           COMPOSITION DURING EXPANSION FROM INFINITE AREA COMBUSTOR

 Pin =    14.7 PSIA
 CASE = Test___________

             REACTANT                    WT FRACTION      ENERGY      TEMP
                                          (SEE NOTE)     KJ/KG-MOL      K  
 FUEL        C3H8O,2propanol              1.0000000   -272700.000    298.150
 OXIDANT     N2O                          1.0000000     82050.000    298.150

 O/F=    3.00000  %FUEL= 25.000000  R,EQ.RATIO= 1.962248  PHI,EQ.RATIO= 2.197160

                 CHAMBER   THROAT     EXIT     EXIT     EXIT     EXIT     EXIT     EXIT
 Pinf/P            1.0000   1.7922   1.0000   5.0000   10.000   15.000   20.000   25.000
 P, BAR            1.0132  0.56537   1.0132  0.20265  0.10132  0.06755  0.05066  0.04053
 T, K             2502.34  2262.50  2502.34  1848.52  1597.01  1464.06  1376.17  1311.61
 RHO, KG/CU M    1.0479-1 6.4931-2 1.0479-1 2.8555-2 1.6530-2 1.2021-2 9.5918-3 8.0512-3
 H, KJ/KG          263.72  -272.31   263.72 -1081.66 -1539.38 -1777.43 -1934.19 -2049.26
 U, KJ/KG         -703.25 -1143.04  -703.25 -1791.34 -2152.35 -2339.36 -2462.37 -2552.67
 G, KJ/KG        -30538.3 -28122.1 -30538.3 -23835.6 -21197.5 -19799.0 -18873.9 -18194.3
 S, KJ/(KG)(K)    12.3093  12.3093  12.3093  12.3093  12.3093  12.3093  12.3093  12.3093

 M, (1/n)          21.516   21.604   21.516   21.657   21.662   21.663   21.663   21.663
 (dLV/dLP)t      -1.00342 -1.00136 -1.00342 -1.00014 -1.00002 -1.00001 -1.00000 -1.00000
 (dLV/dLT)p        1.0785   1.0340   1.0785   1.0043   1.0007   1.0002   1.0001   1.0000
 Cp, KJ/(KG)(K)    2.5690   2.1753   2.5690   1.8586   1.7985   1.7857   1.7825   1.7829
 GAMMAs            1.2071   1.2312   1.2071   1.2629   1.2718   1.2739   1.2745   1.2743
 SON VEL,M/SEC     1080.4   1035.4   1080.4    946.7    882.9    846.1    820.5    800.9
 MACH NUMBER        0.000    1.000     -nan    1.733    2.151    2.388    2.555    2.685

 PERFORMANCE PARAMETERS

 Ae/At                      1.0000     -nan   1.4353   2.1417   2.7679   3.3430   3.8824
 CSTAR, M/SEC               1507.2   1507.2   1507.2   1507.2   1507.2   1507.2   1507.2
 CF                         0.6870     -nan   1.0884   1.2600   1.3406   1.3911   1.4271
 Ivac, M/SEC                1876.4     -nan   2073.0   2221.8   2298.6   2348.5   2384.9
 Isp, M/SEC                 1035.4     -nan   1640.4   1899.0   2020.5   2096.6   2150.8

 MASS FRACTIONS

 *CO              0.31010  0.30675  0.31010  0.29747  0.28774  0.28039  0.27431  0.26907
 *CO2             0.06201  0.06729  0.06201  0.08186  0.09716  0.10871  0.11825  0.12648
 *H               0.00052  0.00022  0.00052  0.00003  0.00000  0.00000  0.00000  0.00000
 *H2              0.01840  0.01886  0.01840  0.01969  0.02041  0.02094  0.02138  0.02176
 H2O              0.12979  0.12899  0.12979  0.12356  0.11733  0.11260  0.10869  0.10532
 *NO              0.00023  0.00005  0.00023  0.00000  0.00000  0.00000  0.00000  0.00000
 *N2              0.47726  0.47734  0.47726  0.47736  0.47736  0.47736  0.47736  0.47736
 *O               0.00005  0.00001  0.00005  0.00000  0.00000  0.00000  0.00000  0.00000
 *OH              0.00160  0.00049  0.00160  0.00003  0.00000  0.00000  0.00000  0.00000
 *O2              0.00003  0.00000  0.00003  0.00000  0.00000  0.00000  0.00000  0.00000

  * THERMODYNAMIC PROPERTIES FITTED TO 20000.K

 NOTE. WEIGHT FRACTION OF FUEL IN TOTAL FUELS AND OF OXIDANT IN TOTAL OXIDANTS

              THEORETICAL ROCKET PERFORMANCE ASSUMING EQUILIBRIUM

           COMPOSITION DURING EXPANSION FROM INFINITE AREA COMBUSTOR

 Pin =    29.4 PSIA
 CASE = Test___________

             REACTANT                    WT FRACTION      ENERGY      TEMP
                                          (SEE NOTE)     KJ/KG-MOL      K  
 FUEL        C3H8O,2propanol              1.0000000   -272700.000    298.150
 OXIDANT     N2O                          1.0000000     82050.000    298.150

 O/F=    3.00000  %FUEL= 25.000000  R,EQ.RATIO= 1.962248  PHI,EQ.RATIO= 2.197160

                 CHAMBER   THROAT     EXIT     EXIT     EXIT     EXIT     EXIT     EXIT
 Pinf/P            1.0000   1.7965   1.0000   5.0000   10.000   15.000   20.000   25.000
 P, BAR            2.0265   1.1280   2.0265  0.40530  0.20265  0.13510  0.10132  0.08106
 T, K             2520.97  2268.74  2520.97  1847.95  1595.73  1462.79  1374.95  1310.44
 RHO, KG/CU M    2.0835-1 1.2929-1 2.0835-1 5.7133-2 3.3087-2 2.4063-2 1.9201-2 1.6117-2
 H, KJ/KG          263.72  -276.62   263.72 -1084.50 -1541.92 -1779.77 -1936.39 -2051.36
 U, KJ/KG         -708.92 -1149.11  -708.92 -1793.90 -2154.39 -2341.20 -2464.10 -2554.31
 G, KJ/KG        -30093.0 -27596.0 -30093.0 -23336.9 -20757.2 -19394.2 -18493.1 -17831.3
 S, KJ/(KG)(K)    12.0417  12.0417  12.0417  12.0417  12.0417  12.0417  12.0417  12.0417

 M, (1/n)          21.550   21.620   21.550   21.659   21.663   21.663   21.663   21.663
 (dLV/dLP)t      -1.00263 -1.00100 -1.00263 -1.00010 -1.00001 -1.00000 -1.00000 -1.00000
 (dLV/dLT)p        1.0599   1.0249   1.0599   1.0030   1.0005   1.0001   1.0001   1.0000
 Cp, KJ/(KG)(K)    2.3988   2.0859   2.3988   1.8439   1.7957   1.7848   1.7822   1.7828
 GAMMAs            1.2166   1.2386   1.2166   1.2648   1.2721   1.2740   1.2745   1.2744
 SON VEL,M/SEC     1087.8   1039.6   1087.8    947.2    882.7    845.7    820.1    800.6
 MACH NUMBER        0.000    1.000     -nan    1.734    2.153    2.390    2.558    2.688

 PERFORMANCE PARAMETERS

 Ae/At                      1.0000     -nan   1.4326   2.1375   2.7628   3.3370   3.8755
 CSTAR, M/SEC               1507.8   1507.8   1507.8   1507.8   1507.8   1507.8   1507.8
 CF                         0.6895     -nan   1.0891   1.2603   1.3408   1.3912   1.4271
 Ivac, M/SEC                1878.9     -nan   2074.1   2222.6   2299.3   2349.2   2385.5
 Isp, M/SEC                 1039.6     -nan   1642.1   1900.3   2021.6   2097.7   2151.8

 MASS FRACTIONS

 *CO              0.31037  0.30689  0.31037  0.29746  0.28767  0.28031  0.27422  0.26897
 *CO2             0.06159  0.06706  0.06159  0.08187  0.09725  0.10883  0.11839  0.12664
 *H               0.00040  0.00016  0.00040  0.00002  0.00000  0.00000  0.00000  0.00000
 *H2              0.01848  0.01890  0.01848  0.01970  0.02042  0.02095  0.02139  0.02177
 H2O              0.13039  0.12924  0.13039  0.12356  0.11729  0.11255  0.10864  0.10526
 *NO              0.00018  0.00004  0.00018  0.00000  0.00000  0.00000  0.00000  0.00000
 *N2              0.47728  0.47734  0.47728  0.47736  0.47736  0.47736  0.47736  0.47736
 *O               0.00003  0.00000  0.00003  0.00000  0.00000  0.00000  0.00000  0.00000
 *OH              0.00125  0.00036  0.00125  0.00002  0.00000  0.00000  0.00000  0.00000
 *O2              0.00002  0.00000  0.00002  0.00000  0.00000  0.00000  0.00000  0.00000

  * THERMODYNAMIC PROPERTIES FITTED TO 20000.K

 NOTE. WEIGHT FRACTION OF FUEL IN TOTAL FUELS AND OF OXIDANT IN TOTAL OXIDANTS

              THEORETICAL ROCKET PERFORMANCE ASSUMING EQUILIBRIUM

           COMPOSITION DURING EXPANSION FROM INFINITE AREA COMBUSTOR

 Pin =    44.1 PSIA
 CASE = Test___________

             REACTANT                    WT FRACTION      ENERGY      TEMP
                                          (SEE NOTE)     KJ/KG-MOL      K  
 FUEL        C3H8O,2propanol              1.0000000   -272700.000    298.150
 OXIDANT     N2O                          1.0000000     82050.000    298.150

 O/F=    3.00000  %FUEL= 25.000000  R,EQ.RATIO= 1.962248  PHI,EQ.RATIO= 2.197160

                 CHAMBER   THROAT     EXIT     EXIT     EXIT     EXIT     EXIT     EXIT
 Pinf/P            1.0000   1.7986   1.0000   5.0000   10.000   15.000   20.000   25.000
 P, BAR            3.0397   1.6900   3.0397  0.60795  0.30397  0.20265  0.15199  0.12159
 T, K             2530.23  2271.60  2530.23  1847.65  1595.13  1462.19  1374.38  1309.89
 RHO, KG/CU M    3.1163-1 1.9353-1 3.1163-1 8.5716-2 4.9650-2 3.6110-2 2.8813-2 2.4185-2
 H, KJ/KG          263.72  -278.71   263.72 -1085.84 -1543.12 -1780.87 -1937.42 -2052.35
 U, KJ/KG         -711.73 -1152.01  -711.73 -1795.10 -2155.35 -2342.07 -2464.92 -2555.09
 G, KJ/KG        -29808.7 -27277.3 -29808.7 -23045.7 -20501.6 -19159.4 -18272.3 -17620.8
 S, KJ/(KG)(K)    11.8853  11.8853  11.8853  11.8853  11.8853  11.8853  11.8853  11.8853

 M, (1/n)          21.567   21.627   21.567   21.660   21.663   21.663   21.663   21.663
 (dLV/dLP)t      -1.00224 -1.00083 -1.00224 -1.00008 -1.00001 -1.00000 -1.00000 -1.00000
 (dLV/dLT)p        1.0508   1.0206   1.0508   1.0025   1.0004   1.0001   1.0000   1.0000
 Cp, KJ/(KG)(K)    2.3163   2.0446   2.3163   1.8375   1.7945   1.7844   1.7820   1.7828
 GAMMAs            1.2218   1.2423   1.2218   1.2656   1.2723   1.2741   1.2745   1.2744
 SON VEL,M/SEC     1091.7   1041.6   1091.7    947.4    882.6    845.6    819.9    800.4
 MACH NUMBER        0.000    1.000     -nan    1.734    2.154    2.391    2.559    2.689

 PERFORMANCE PARAMETERS

 Ae/At                      1.0000     -nan   1.4314   2.1356   2.7604   3.3342   3.8724
 CSTAR, M/SEC               1508.0   1508.0   1508.0   1508.0   1508.0   1508.0   1508.0
 CF                         0.6907     -nan   1.0894   1.2606   1.3409   1.3913   1.4272
 Ivac, M/SEC                1880.0     -nan   2074.6   2223.0   2299.7   2349.6   2385.8
 Isp, M/SEC                 1041.6     -nan   1642.9   1901.0   2022.2   2098.2   2152.2

 MASS FRACTIONS

 *CO              0.31050  0.30696  0.31050  0.29746  0.28765  0.28027  0.27418  0.26892
 *CO2             0.06138  0.06696  0.06138  0.08188  0.09730  0.10889  0.11846  0.12672
 *H               0.00034  0.00013  0.00034  0.00001  0.00000  0.00000  0.00000  0.00000
 *H2              0.01851  0.01892  0.01851  0.01970  0.02042  0.02095  0.02139  0.02177
 H2O              0.13070  0.12935  0.13070  0.12356  0.11727  0.11252  0.10861  0.10523
 *NO              0.00016  0.00003  0.00016  0.00000  0.00000  0.00000  0.00000  0.00000
 *N2              0.47729  0.47735  0.47729  0.47736  0.47736  0.47736  0.47736  0.47736
 *O               0.00002  0.00000  0.00002  0.00000  0.00000  0.00000  0.00000  0.00000
 *OH              0.00108  0.00030  0.00108  0.00001  0.00000  0.00000  0.00000  0.00000
 *O2              0.00001  0.00000  0.00001  0.00000  0.00000  0.00000  0.00000  0.00000

  * THERMODYNAMIC PROPERTIES FITTED TO 20000.K

 NOTE. WEIGHT FRACTION OF FUEL IN TOTAL FUELS AND OF OXIDANT IN TOTAL OXIDANTS

              THEORETICAL ROCKET PERFORMANCE ASSUMING EQUILIBRIUM

           COMPOSITION DURING EXPANSION FROM INFINITE AREA COMBUSTOR

 Pin =    58.8 PSIA
 CASE = Test___________

             REACTANT                    WT FRACTION      ENERGY      TEMP
                                          (SEE NOTE)     KJ/KG-MOL      K  
 FUEL        C3H8O,2propanol              1.0000000   -272700.000    298.150
 OXIDANT     N2O                          1.0000000     82050.000    298.150

 O/F=    3.00000  %FUEL= 25.000000  R,EQ.RATIO= 1.962248  PHI,EQ.RATIO= 2.197160

                 CHAMBER   THROAT     EXIT     EXIT     EXIT     EXIT     EXIT     EXIT
 Pinf/P            1.0000   1.7999   1.0000   5.0000   10.000   15.000   20.000   25.000
 P, BAR            4.0530   2.2517   4.0530  0.81060  0.40530  0.27020  0.20265  0.16212
 T, K             2536.09  2273.33  2536.09  1847.46  1594.75  1461.82  1374.02  1309.55
 RHO, KG/CU M    4.1475-1 2.5770-1 4.1475-1 1.1430-1 6.6216-2 4.8159-2 3.8427-2 3.2255-2
 H, KJ/KG          263.72  -280.02   263.72 -1086.67 -1543.86 -1781.55 -1938.06 -2052.95
 U, KJ/KG         -713.51 -1153.80  -713.51 -1795.84 -2155.94 -2342.61 -2465.42 -2555.57
 G, KJ/KG        -29597.3 -27047.1 -29597.3 -22839.4 -20321.1 -18993.6 -18116.4 -17472.1
 S, KJ/(KG)(K)    11.7744  11.7744  11.7744  11.7744  11.7744  11.7744  11.7744  11.7744

 M, (1/n)          21.578   21.632   21.578   21.660   21.663   21.663   21.663   21.663
 (dLV/dLP)t      -1.00199 -1.00073 -1.00199 -1.00007 -1.00001 -1.00000 -1.00000 -1.00000
 (dLV/dLT)p        1.0450   1.0180   1.0450   1.0021   1.0003   1.0001   1.0000   1.0000
 Cp, KJ/(KG)(K)    2.2646   2.0195   2.2646   1.8336   1.7938   1.7842   1.7819   1.7827
 GAMMAs            1.2252   1.2446   1.2252   1.2661   1.2724   1.2741   1.2745   1.2744
 SON VEL,M/SEC     1094.2   1042.8   1094.2    947.6    882.5    845.5    819.8    800.3
 MACH NUMBER        0.000    1.000     -nan    1.734    2.154    2.392    2.560    2.690

 PERFORMANCE PARAMETERS

 Ae/At                      1.0000     -nan   1.4306   2.1345   2.7590   3.3326   3.8706
 CSTAR, M/SEC               1508.2   1508.2   1508.2   1508.2   1508.2   1508.2   1508.2
 CF                         0.6915     -nan   1.0897   1.2607   1.3410   1.3914   1.4272
 Ivac, M/SEC                1880.7     -nan   2074.9   2223.3   2299.9   2349.8   2386.0
 Isp, M/SEC                 1042.8     -nan   1643.4   1901.4   2022.5   2098.5   2152.5

 MASS FRACTIONS

 *CO              0.31058  0.30700  0.31058  0.29745  0.28763  0.28024  0.27415  0.26889
 *CO2             0.06126  0.06689  0.06126  0.08189  0.09733  0.10893  0.11850  0.12677
 *H               0.00030  0.00012  0.00030  0.00001  0.00000  0.00000  0.00000  0.00000
 *H2              0.01854  0.01893  0.01854  0.01970  0.02042  0.02095  0.02139  0.02177
 H2O              0.13089  0.12942  0.13089  0.12356  0.11726  0.11251  0.10859  0.10521
 *NO              0.00014  0.00003  0.00014  0.00000  0.00000  0.00000  0.00000  0.00000
 *N2              0.47729  0.47735  0.47729  0.47736  0.47736  0.47736  0.47736  0.47736
 *O               0.00002  0.00000  0.00002  0.00000  0.00000  0.00000  0.00000  0.00000
 *OH              0.00096  0.00026  0.00096  0.00001  0.00000  0.00000  0.00000  0.00000
 *O2              0.00001  0.00000  0.00001  0.00000  0.00000  0.00000  0.00000  0.00000

  * THERMODYNAMIC PROPERTIES FITTED TO 20000.K

 NOTE. WEIGHT FRACTION OF FUEL IN TOTAL FUELS AND OF OXIDANT IN TOTAL OXIDANTS

              THEORETICAL ROCKET PERFORMANCE ASSUMING EQUILIBRIUM

           COMPOSITION DURING EXPANSION FROM INFINITE AREA COMBUSTOR

 Pin =    73.5 PSIA
 CASE = Test___________

             REACTANT                    WT FRACTION      ENERGY      TEMP
                                          (SEE NOTE)     KJ/KG-MOL      K  
 FUEL        C3H8O,2propanol              1.0000000   -272700.000    298.150
 OXIDANT     N2O                          1.0000000     82050.000    298.150

 O/F=    3.00000  %FUEL= 25.000000  R,EQ.RATIO= 1.962248  PHI,EQ.RATIO= 2.197160

                 CHAMBER   THROAT     EXIT     EXIT     EXIT     EXIT     EXIT     EXIT
 Pinf/P            1.0000   1.8009   1.0000   5.0000   10.000   15.000   20.000   25.000
 P, BAR            5.0663   2.8132   5.0663   1.0132  0.50662  0.33775  0.25331  0.20265
 T, K             2540.26  2274.52  2540.26  1847.32  1594.49  1461.56  1373.78  1309.31
 RHO, KG/CU M    5.1776-1 3.2184-1 5.1776-1 1.4289-1 8.2784-2 6.0210-2 4.8043-2 4.0327-2
 H, KJ/KG          263.72  -280.94   263.72 -1087.25 -1544.37 -1782.02 -1938.51 -2053.38
 U, KJ/KG         -714.77 -1155.06  -714.77 -1796.35 -2156.36 -2342.98 -2465.77 -2555.90
 G, KJ/KG        -29428.0 -26866.6 -29428.0 -22679.5 -20181.4 -18865.4 -17995.8 -17357.2
 S, KJ/(KG)(K)    11.6884  11.6884  11.6884  11.6884  11.6884  11.6884  11.6884  11.6884

 M, (1/n)          21.585   21.635   21.585   21.661   21.663   21.663   21.663   21.663
 (dLV/dLP)t      -1.00181 -1.00065 -1.00181 -1.00007 -1.00001 -1.00000 -1.00000 -1.00000
 (dLV/dLT)p        1.0409   1.0162   1.0409   1.0019   1.0003   1.0001   1.0000   1.0000
 Cp, KJ/(KG)(K)    2.2281   2.0021   2.2281   1.8310   1.7933   1.7841   1.7819   1.7827
 GAMMAs            1.2278   1.2462   1.2278   1.2664   1.2725   1.2742   1.2745   1.2744
 SON VEL,M/SEC     1096.1   1043.7   1096.1    947.6    882.5    845.4    819.8    800.3
 MACH NUMBER        0.000    1.000     -nan    1.735    2.155    2.393    2.560    2.690

 PERFORMANCE PARAMETERS

 Ae/At                      1.0000     -nan   1.4301   2.1337   2.7581   3.3315   3.8693
 CSTAR, M/SEC               1508.2   1508.2   1508.2   1508.2   1508.2   1508.2   1508.2
 CF                         0.6920     -nan   1.0898   1.2608   1.3411   1.3915   1.4273
 Ivac, M/SEC                1881.2     -nan   2075.1   2223.4   2300.1   2349.9   2386.2
 Isp, M/SEC                 1043.7     -nan   1643.8   1901.6   2022.7   2098.7   2152.7

 MASS FRACTIONS

 *CO              0.31064  0.30702  0.31064  0.29745  0.28762  0.28023  0.27413  0.26887
 *CO2             0.06116  0.06685  0.06116  0.08189  0.09735  0.10895  0.11853  0.12680
 *H               0.00028  0.00011  0.00028  0.00001  0.00000  0.00000  0.00000  0.00000
 *H2              0.01855  0.01894  0.01855  0.01971  0.02042  0.02096  0.02139  0.02177
 H2O              0.13102  0.12946  0.13102  0.12356  0.11725  0.11250  0.10858  0.10519
 *NO              0.00013  0.00003  0.00013  0.00000  0.00000  0.00000  0.00000  0.00000
 *N2              0.47730  0.47735  0.47730  0.47736  0.47736  0.47736  0.47736  0.47736
 *O               0.00001  0.00000  0.00001  0.00000  0.00000  0.00000  0.00000  0.00000
 *OH              0.00088  0.00024  0.00088  0.00001  0.00000  0.00000  0.00000  0.00000
 *O2              0.00001  0.00000  0.00001  0.00000  0.00000  0.00000  0.00000  0.00000

  * THERMODYNAMIC PROPERTIES FITTED TO 20000.K

 NOTE. WEIGHT FRACTION OF FUEL IN TOTAL FUELS AND OF OXIDANT IN TOTAL OXIDANTS

              THEORETICAL ROCKET PERFORMANCE ASSUMING EQUILIBRIUM

           COMPOSITION DURING EXPANSION FROM INFINITE AREA COMBUSTOR

 Pin =    88.2 PSIA
 CASE = Test___________

             REACTANT                    WT FRACTION      ENERGY      TEMP
                                          (SEE NOTE)     KJ/KG-MOL      K  
 FUEL        C3H8O,2propanol              1.0000000   -272700.000    298.150
 OXIDANT     N2O                          1.0000000     82050.000    298.150

 O/F=    3.00000  %FUEL= 25.000000  R,EQ.RATIO= 1.962248  PHI,EQ.RATIO= 2.197160

                 CHAMBER   THROAT     EXIT     EXIT     EXIT     EXIT     EXIT     EXIT
 Pinf/P            1.0000   1.8016   1.0000   5.0000   10.000   15.000   20.000   25.000
 P, BAR            6.0795   3.3745   6.0795   1.2159  0.60795  0.40530  0.30397  0.24318
 T, K             2543.44  2275.41  2543.44  1847.21  1594.29  1461.37  1373.59  1309.14
 RHO, KG/CU M    6.2071-1 3.8594-1 6.2071-1 1.7148-1 9.9353-2 7.2261-2 5.7659-2 4.8398-2
 H, KJ/KG          263.72  -281.64   263.72 -1087.68 -1544.76 -1782.38 -1938.84 -2053.70
 U, KJ/KG         -715.73 -1156.00  -715.73 -1796.73 -2156.67 -2343.26 -2466.03 -2556.15
 G, KJ/KG        -29286.5 -26717.9 -29286.5 -22549.0 -20067.6 -18760.9 -17897.5 -17263.5
 S, KJ/(KG)(K)    11.6182  11.6182  11.6182  11.6182  11.6182  11.6182  11.6182  11.6182

 M, (1/n)          21.591   21.637   21.591   21.661   21.663   21.663   21.663   21.663
 (dLV/dLP)t      -1.00168 -1.00060 -1.00168 -1.00006 -1.00001 -1.00000 -1.00000 -1.00000
 (dLV/dLT)p        1.0378   1.0149   1.0378   1.0017   1.0003   1.0001   1.0000   1.0000
 Cp, KJ/(KG)(K)    2.2006   1.9891   2.2006   1.8290   1.7930   1.7840   1.7818   1.7827
 GAMMAs            1.2297   1.2474   1.2297   1.2667   1.2725   1.2742   1.2746   1.2744
 SON VEL,M/SEC     1097.5   1044.4   1097.5    947.7    882.4    845.4    819.7    800.2
 MACH NUMBER        0.000    1.000    0.000    1.735    2.155    2.393    2.560    2.690

 PERFORMANCE PARAMETERS

 Ae/At                      1.0000 1029160.   1.4297   2.1332   2.7574   3.3307   3.8684
 CSTAR, M/SEC               1508.3   1508.3   1508.3   1508.3   1508.3   1508.3   1508.3
 CF                         0.6924   0.0000   1.0900   1.2609   1.3412   1.3915   1.4273
 Ivac, M/SEC                1881.6*********   2075.3   2223.6   2300.2   2350.0   2386.3
 Isp, M/SEC                 1044.4      0.0   1644.0   1901.8   2022.9   2098.8   2152.9

 MASS FRACTIONS

 *CO              0.31068  0.30704  0.31068  0.29745  0.28761  0.28022  0.27412  0.26886
 *CO2             0.06110  0.06682  0.06110  0.08190  0.09736  0.10897  0.11856  0.12682
 *H               0.00026  0.00010  0.00026  0.00001  0.00000  0.00000  0.00000  0.00000
 *H2              0.01857  0.01894  0.01857  0.01971  0.02042  0.02096  0.02140  0.02177
 H2O              0.13113  0.12950  0.13113  0.12356  0.11724  0.11249  0.10857  0.10518
 *NO              0.00012  0.00002  0.00012  0.00000  0.00000  0.00000  0.00000  0.00000
 *N2              0.47730  0.47735  0.47730  0.47736  0.47736  0.47736  0.47736  0.47736
 *O               0.00001  0.00000  0.00001  0.00000  0.00000  0.00000  0.00000  0.00000
 *OH              0.00082  0.00022  0.00082  0.00001  0.00000  0.00000  0.00000  0.00000
 *O2              0.00001  0.00000  0.00001  0.00000  0.00000  0.00000  0.00000  0.00000

  * THERMODYNAMIC PROPERTIES FITTED TO 20000.K

 NOTE. WEIGHT FRACTION OF FUEL IN TOTAL FUELS AND OF OXIDANT IN TOTAL OXIDANTS

              THEORETICAL ROCKET PERFORMANCE ASSUMING EQUILIBRIUM

           COMPOSITION DURING EXPANSION FROM INFINITE AREA COMBUSTOR

 Pin =   102.9 PSIA
 CASE = Test___________

             REACTANT                    WT FRACTION      ENERGY      TEMP
                                          (SEE NOTE)     KJ/KG-MOL      K  
 FUEL        C3H8O,2propanol              1.0000000   -272700.000    298.150
 OXIDANT     N2O                          1.0000000     82050.000    298.150

 O/F=    3.00000  %FUEL= 25.000000  R,EQ.RATIO= 1.962248  PHI,EQ.RATIO= 2.197160

                 CHAMBER   THROAT     EXIT     EXIT     EXIT     EXIT     EXIT     EXIT
 Pinf/P            1.0000   1.8021   1.0000   5.0000   10.000   15.000   20.000   25.000
 P, BAR            7.0927   3.9357   7.0927   1.4185  0.70927  0.47285  0.35464  0.28371
 T, K             2545.96  2276.11  2545.96  1847.12  1594.14  1461.21  1373.44  1309.00
 RHO, KG/CU M    7.2360-1 4.5003-1 7.2360-1 2.0007-1 1.1592-1 8.4313-2 6.7276-2 5.6471-2
 H, KJ/KG          263.72  -282.19   263.72 -1088.02 -1545.06 -1782.66 -1939.10 -2053.95
 U, KJ/KG         -716.49 -1156.74  -716.49 -1797.03 -2156.91 -2343.48 -2466.24 -2556.35
 G, KJ/KG        -29164.7 -26591.4 -29164.7 -22438.7 -19971.5 -18672.6 -17814.6 -17184.5
 S, KJ/(KG)(K)    11.5589  11.5589  11.5589  11.5589  11.5589  11.5589  11.5589  11.5589
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

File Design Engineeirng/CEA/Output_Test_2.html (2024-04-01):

         NASA-GLENN CHEMICAL EQUILIBRIUM PROGRAM CEA2, FEBRUARY 5, 2004
                   BY  BONNIE MCBRIDE AND SANFORD GORDON
      REFS: NASA RP-1311, PART I, 1994 AND NASA RP-1311, PART II, 1996

 *******************************************************************************

 ### CEA analysis performed on Thu 14-Mar-2024 14:53:27
  
 # Problem Type: "Rocket" (Infinite Area Combustor)
  
 prob case=Test___________9648 ro equilibrium
  
 # Pressure (5 values):
 p,bar= 3, 6, 9, 12, 15
 # Chamber/Exit Pressure Ratio (5 values):
 pi/p= 3, 6, 9, 12, 15
  
 # Oxidizer/Fuel Wt. ratio (9 values):
 o/f= 3, 3.5, 4, 4.5, 5, 5.5, 6, 6.5, 7
  
 # You selected the following fuels and oxidizers:
 reac
 fuel C3H8O,2propanol   wt%=100.0000  t,k= 298.150
 oxid N2O               wt%=100.0000  t,k= 298.150
  
 # You selected these options for output:
 # short version of output
 output short
 # Proportions of any products will be expressed as Mass Fractions.
 output massf
 # Heat will be expressed as siunits
 output siunits
  
 # Input prepared by this script:/var/www/sites/cearun.grc.nasa.gov/cgi-bin/CEARU
 N/prepareInputFile.cgi
  
 ### IMPORTANT:  The following line is the end of your CEA input file!
 end

              THEORETICAL ROCKET PERFORMANCE ASSUMING EQUILIBRIUM

           COMPOSITION DURING EXPANSION FROM INFINITE AREA COMBUSTOR

 Pin =    43.5 PSIA
 CASE = Test___________

             REACTANT                    WT FRACTION      ENERGY      TEMP
                                          (SEE NOTE)     KJ/KG-MOL      K  
 FUEL        C3H8O,2propanol              1.0000000   -272700.000    298.150
 OXIDANT     N2O                          1.0000000     82050.000    298.150

 O/F=    3.00000  %FUEL= 25.000000  R,EQ.RATIO= 1.962248  PHI,EQ.RATIO= 2.197160

                 CHAMBER   THROAT     EXIT     EXIT     EXIT     EXIT     EXIT
 Pinf/P            1.0000   1.7986   3.0000   6.0000   9.0000   12.000   15.000
 P, BAR            3.0000   1.6680   1.0000  0.50000  0.33333  0.25000  0.20000
 T, K             2529.94  2271.51  2053.07  1778.18  1631.47  1534.02  1462.21
 RHO, KG/CU M    3.0758-1 1.9101-1 1.2683-1 7.3255-2 5.3232-2 4.2461-2 3.5637-2
 H, KJ/KG          263.72  -278.65  -703.53 -1212.67 -1477.85 -1652.56 -1780.84
 U, KJ/KG         -711.64 -1151.92 -1491.97 -1895.21 -2104.04 -2241.33 -2342.05
 G, KJ/KG        -29818.2 -27287.7 -25115.3 -22355.8 -20876.6 -19892.7 -19167.0
 S, KJ/(KG)(K)    11.8904  11.8904  11.8904  11.8904  11.8904  11.8904  11.8904

 M, (1/n)          21.567   21.627   21.651   21.661   21.663   21.663   21.663
 (dLV/dLP)t      -1.00225 -1.00083 -1.00029 -1.00005 -1.00002 -1.00001 -1.00000
 (dLV/dLT)p        1.0510   1.0207   1.0078   1.0016   1.0005   1.0002   1.0001
 Cp, KJ/(KG)(K)    2.3188   2.0459   1.9094   1.8220   1.7987   1.7890   1.7844
 GAMMAs            1.2216   1.2422   1.2563   1.2679   1.2716   1.2733   1.2741
 SON VEL,M/SEC     1091.6   1041.5    995.2    930.3    892.3    865.8    845.6
 MACH NUMBER        0.000    1.000    1.398    1.847    2.091    2.261    2.391

 PERFORMANCE PARAMETERS

 Ae/At                      1.0000   1.1277   1.5804   2.0024   2.3932   2.7605
 CSTAR, M/SEC               1508.0   1508.0   1508.0   1508.0   1508.0   1508.0
 CF                         0.6906   0.9223   1.1395   1.2376   1.2982   1.3409
 Ivac, M/SEC                1880.0   1957.7   2115.6   2201.8   2258.4   2299.7
 Isp, M/SEC                 1041.5   1390.9   1718.4   1866.3   1957.7   2022.2

 MASS FRACTIONS

 *CO              0.31050  0.30695  0.30283  0.29518  0.28935  0.28449  0.28027
 *CO2             0.06139  0.06696  0.07344  0.08546  0.09462  0.10225  0.10889
 *H               0.00034  0.00014  0.00005  0.00001  0.00000  0.00000  0.00000
 *H2              0.01851  0.01892  0.01929  0.01987  0.02030  0.02065  0.02095
 H2O              0.13069  0.12935  0.12695  0.12211  0.11837  0.11524  0.11253
 *NO              0.00016  0.00003  0.00001  0.00000  0.00000  0.00000  0.00000
 *N2              0.47729  0.47735  0.47736  0.47736  0.47736  0.47736  0.47736
 *O               0.00002  0.00000  0.00000  0.00000  0.00000  0.00000  0.00000
 *OH              0.00108  0.00030  0.00008  0.00001  0.00000  0.00000  0.00000
 *O2              0.00001  0.00000  0.00000  0.00000  0.00000  0.00000  0.00000

  * THERMODYNAMIC PROPERTIES FITTED TO 20000.K

 NOTE. WEIGHT FRACTION OF FUEL IN TOTAL FUELS AND OF OXIDANT IN TOTAL OXIDANTS

              THEORETICAL ROCKET PERFORMANCE ASSUMING EQUILIBRIUM

           COMPOSITION DURING EXPANSION FROM INFINITE AREA COMBUSTOR

 Pin =    87.0 PSIA
 CASE = Test___________

             REACTANT                    WT FRACTION      ENERGY      TEMP
                                          (SEE NOTE)     KJ/KG-MOL      K  
 FUEL        C3H8O,2propanol              1.0000000   -272700.000    298.150
 OXIDANT     N2O                          1.0000000     82050.000    298.150

 O/F=    3.00000  %FUEL= 25.000000  R,EQ.RATIO= 1.962248  PHI,EQ.RATIO= 2.197160

                 CHAMBER   THROAT     EXIT     EXIT     EXIT     EXIT     EXIT
 Pinf/P            1.0000   1.8015   3.0000   6.0000   9.0000   12.000   15.000
 P, BAR            6.0000   3.3305   2.0000   1.0000  0.66667  0.50000  0.40000
 T, K             2543.22  2275.35  2054.00  1777.53  1630.65  1533.18  1461.38
 RHO, KG/CU M    6.1263-1 3.8092-1 2.5359-1 1.4657-1 1.0652-1 8.4969-2 7.1315-2
 H, KJ/KG          263.72  -281.59  -705.40 -1214.47 -1479.53 -1654.14 -1782.35
 U, KJ/KG         -715.66 -1155.93 -1494.06 -1896.75 -2105.39 -2242.59 -2343.24
 G, KJ/KG        -29296.8 -26728.6 -24579.7 -21875.3 -20433.0 -19474.7 -18768.4
 S, KJ/(KG)(K)    11.6233  11.6233  11.6233  11.6233  11.6233  11.6233  11.6233

 M, (1/n)          21.591   21.637   21.654   21.662   21.663   21.663   21.663
 (dLV/dLP)t      -1.00169 -1.00061 -1.00021 -1.00004 -1.00001 -1.00001 -1.00000
 (dLV/dLT)p        1.0381   1.0150   1.0056   1.0011   1.0004   1.0002   1.0001
 Cp, KJ/(KG)(K)    2.2025   1.9900   1.8857   1.8164   1.7966   1.7880   1.7840
 GAMMAs            1.2296   1.2474   1.2590   1.2686   1.2719   1.2734   1.2742
 SON VEL,M/SEC     1097.4   1044.3    996.4    930.4    892.2    865.6    845.4
 MACH NUMBER        0.000    1.000    1.397    1.848    2.093    2.262    2.393

 PERFORMANCE PARAMETERS

 Ae/At                      1.0000   1.1267   1.5785   2.0001   2.3905   2.7574
 CSTAR, M/SEC               1508.3   1508.3   1508.3   1508.3   1508.3   1508.3
 CF                         0.6924   0.9230   1.1400   1.2380   1.2985   1.3412
 Ivac, M/SEC                1881.6   1958.7   2116.2   2202.4   2259.0   2300.2
 Isp, M/SEC                 1044.3   1392.2   1719.4   1867.2   1958.5   2022.9

 MASS FRACTIONS

 *CO              0.31068  0.30704  0.30287  0.29516  0.28932  0.28445  0.28022
 *CO2             0.06110  0.06682  0.07339  0.08549  0.09468  0.10232  0.10897
 *H               0.00026  0.00010  0.00003  0.00001  0.00000  0.00000  0.00000
 *H2              0.01857  0.01894  0.01930  0.01988  0.02030  0.02065  0.02096
 H2O              0.13112  0.12950  0.12700  0.12210  0.11834  0.11521  0.11249
 *NO              0.00012  0.00002  0.00000  0.00000  0.00000  0.00000  0.00000
 *N2              0.47730  0.47735  0.47736  0.47736  0.47736  0.47736  0.47736
 *O               0.00001  0.00000  0.00000  0.00000  0.00000  0.00000  0.00000
 *OH              0.00082  0.00022  0.00005  0.00001  0.00000  0.00000  0.00000
 *O2              0.00001  0.00000  0.00000  0.00000  0.00000  0.00000  0.00000

  * THERMODYNAMIC PROPERTIES FITTED TO 20000.K

 NOTE. WEIGHT FRACTION OF FUEL IN TOTAL FUELS AND OF OXIDANT IN TOTAL OXIDANTS

              THEORETICAL ROCKET PERFORMANCE ASSUMING EQUILIBRIUM

           COMPOSITION DURING EXPANSION FROM INFINITE AREA COMBUSTOR

 Pin =   130.5 PSIA
 CASE = Test___________

             REACTANT                    WT FRACTION      ENERGY      TEMP
                                          (SEE NOTE)     KJ/KG-MOL      K  
 FUEL        C3H8O,2propanol              1.0000000   -272700.000    298.150
 OXIDANT     N2O                          1.0000000     82050.000    298.150

 O/F=    3.00000  %FUEL= 25.000000  R,EQ.RATIO= 1.962248  PHI,EQ.RATIO= 2.197160

                 CHAMBER   THROAT     EXIT     EXIT     EXIT     EXIT     EXIT
 Pinf/P            1.0000   1.8029   3.0000   6.0000   9.0000   12.000   15.000
 P, BAR            9.0000   4.9919   3.0000   1.5000   1.0000  0.75000  0.60000
 T, K             2549.59  2277.09  2054.40  1777.23  1630.26  1532.79  1461.00
 RHO, KG/CU M    9.1715-1 5.7062-1 3.8035-1 2.1989-1 1.5982-1 1.2749-1 1.0700-1
 H, KJ/KG          263.72  -282.97  -706.26 -1215.31 -1480.30 -1654.88 -1783.05
 U, KJ/KG         -717.59 -1157.80 -1495.02 -1897.45 -2106.02 -2243.18 -2343.79
 G, KJ/KG        -28972.9 -26394.7 -24264.5 -21595.1 -20174.8 -19231.7 -18536.6
 S, KJ/(KG)(K)    11.4672  11.4672  11.4672  11.4672  11.4672  11.4672  11.4672

 M, (1/n)          21.602   21.642   21.656   21.662   21.663   21.663   21.663
 (dLV/dLP)t      -1.00142 -1.00050 -1.00017 -1.00003 -1.00001 -1.00001 -1.00000
 (dLV/dLT)p        1.0319   1.0123   1.0046   1.0009   1.0003   1.0001   1.0001
 Cp, KJ/(KG)(K)    2.1475   1.9647   1.8750   1.8139   1.7957   1.7876   1.7838
 GAMMAs            1.2337   1.2498   1.2602   1.2690   1.2720   1.2735   1.2742
 SON VEL,M/SEC     1100.3   1045.7    997.0    930.4    892.2    865.6    845.3
 MACH NUMBER        0.000    1.000    1.397    1.849    2.093    2.263    2.394

 PERFORMANCE PARAMETERS

 Ae/At                      1.0000   1.1263   1.5777   1.9990   2.3892   2.7561
 CSTAR, M/SEC               1508.4   1508.4   1508.4   1508.4   1508.4   1508.4
 CF                         0.6932   0.9234   1.1402   1.2382   1.2987   1.3413
 Ivac, M/SEC                1882.3   1959.1   2116.5   2202.7   2259.2   2300.4
 Isp, M/SEC                 1045.7   1392.8   1719.9   1867.6   1958.9   2023.3

 MASS FRACTIONS

 *CO              0.31077  0.30708  0.30288  0.29515  0.28930  0.28443  0.28019
 *CO2             0.06096  0.06676  0.07336  0.08550  0.09470  0.10236  0.10901
 *H               0.00022  0.00008  0.00003  0.00001  0.00000  0.00000  0.00000
 *H2              0.01859  0.01895  0.01930  0.01988  0.02030  0.02065  0.02096
 H2O              0.13133  0.12957  0.12702  0.12209  0.11833  0.11520  0.11248
 *NO              0.00010  0.00002  0.00000  0.00000  0.00000  0.00000  0.00000
 *N2              0.47731  0.47735  0.47736  0.47736  0.47736  0.47736  0.47736
 *O               0.00001  0.00000  0.00000  0.00000  0.00000  0.00000  0.00000
 *OH              0.00070  0.00018  0.00004  0.00000  0.00000  0.00000  0.00000
 *O2              0.00001  0.00000  0.00000  0.00000  0.00000  0.00000  0.00000

  * THERMODYNAMIC PROPERTIES FITTED TO 20000.K

 NOTE. WEIGHT FRACTION OF FUEL IN TOTAL FUELS AND OF OXIDANT IN TOTAL OXIDANTS

              THEORETICAL ROCKET PERFORMANCE ASSUMING EQUILIBRIUM

           COMPOSITION DURING EXPANSION FROM INFINITE AREA COMBUSTOR

 Pin =   174.0 PSIA
 CASE = Test___________

             REACTANT                    WT FRACTION      ENERGY      TEMP
                                          (SEE NOTE)     KJ/KG-MOL      K  
 FUEL        C3H8O,2propanol              1.0000000   -272700.000    298.150
 OXIDANT     N2O                          1.0000000     82050.000    298.150

 O/F=    3.00000  %FUEL= 25.000000  R,EQ.RATIO= 1.962248  PHI,EQ.RATIO= 2.197160

                 CHAMBER   THROAT     EXIT     EXIT     EXIT     EXIT     EXIT
 Pinf/P            1.0000   1.8038   3.0000   6.0000   9.0000   12.000   15.000
 P, BAR            12.000   6.6527   4.0000   2.0000   1.3333   1.0000  0.80000
 T, K             2553.56  2278.13  2054.64  1777.04  1630.03  1532.55  1460.77
 RHO, KG/CU M    1.2214 0 7.6021-1 5.0709-1 2.9322-1 2.1312-1 1.7001-1 1.4269-1
 H, KJ/KG          263.72  -283.82  -706.79 -1215.81 -1480.78 -1655.32 -1783.48
 U, KJ/KG         -718.78 -1158.93 -1495.60 -1897.89 -2106.40 -2243.53 -2344.13
 G, KJ/KG        -28735.7 -26155.4 -24040.3 -21396.7 -19992.2 -19059.7 -18372.6
 S, KJ/(KG)(K)    11.3565  11.3565  11.3565  11.3565  11.3565  11.3565  11.3565

 M, (1/n)          21.610   21.645   21.657   21.662   21.663   21.663   21.663
 (dLV/dLP)t      -1.00125 -1.00044 -1.00015 -1.00003 -1.00001 -1.00001 -1.00001
 (dLV/dLT)p        1.0280   1.0107   1.0040   1.0008   1.0003   1.0001   1.0001
 Cp, KJ/(KG)(K)    2.1136   1.9493   1.8687   1.8124   1.7952   1.7874   1.7836
 GAMMAs            1.2363   1.2514   1.2609   1.2692   1.2721   1.2735   1.2742
 SON VEL,M/SEC     1102.1   1046.5    997.3    930.4    892.1    865.5    845.2
 MACH NUMBER        0.000    1.000    1.397    1.849    2.094    2.264    2.394

 PERFORMANCE PARAMETERS

 Ae/At                      1.0000   1.1260   1.5772   1.9984   2.3885   2.7553
 CSTAR, M/SEC               1508.4   1508.4   1508.4   1508.4   1508.4   1508.4
 CF                         0.6937   0.9236   1.1404   1.2383   1.2988   1.3414
 Ivac, M/SEC                1882.7   1959.4   2116.7   2202.8   2259.3   2300.5
 Isp, M/SEC                 1046.5   1393.2   1720.2   1867.9   1959.1   2023.5

 MASS FRACTIONS

 *CO              0.31082  0.30710  0.30289  0.29515  0.28929  0.28441  0.28018
 *CO2             0.06088  0.06672  0.07335  0.08551  0.09472  0.10238  0.10903
 *H               0.00019  0.00007  0.00002  0.00000  0.00000  0.00000  0.00000
 *H2              0.01861  0.01896  0.01930  0.01988  0.02030  0.02065  0.02096
 H2O              0.13146  0.12961  0.12703  0.12209  0.11833  0.11519  0.11247
 NH3              0.00001  0.00000  0.00000  0.00000  0.00000  0.00000  0.00000
 *NO              0.00009  0.00002  0.00000  0.00000  0.00000  0.00000  0.00000
 *N2              0.47731  0.47735  0.47736  0.47736  0.47736  0.47736  0.47736
 *O               0.00001  0.00000  0.00000  0.00000  0.00000  0.00000  0.00000
 *OH              0.00062  0.00016  0.00004  0.00000  0.00000  0.00000  0.00000

  * THERMODYNAMIC PROPERTIES FITTED TO 20000.K

 NOTE. WEIGHT FRACTION OF FUEL IN TOTAL FUELS AND OF OXIDANT IN TOTAL OXIDANTS

              THEORETICAL ROCKET PERFORMANCE ASSUMING EQUILIBRIUM

           COMPOSITION DURING EXPANSION FROM INFINITE AREA COMBUSTOR

 Pin =   217.6 PSIA
 CASE = Test___________

             REACTANT                    WT FRACTION      ENERGY      TEMP
                                          (SEE NOTE)     KJ/KG-MOL      K  
 FUEL        C3H8O,2propanol              1.0000000   -272700.000    298.150
 OXIDANT     N2O                          1.0000000     82050.000    298.150

 O/F=    3.00000  %FUEL= 25.000000  R,EQ.RATIO= 1.962248  PHI,EQ.RATIO= 2.197160

                 CHAMBER   THROAT     EXIT     EXIT     EXIT     EXIT     EXIT
 Pinf/P            1.0000   1.8044   3.0000   6.0000   9.0000   12.000   15.000
 P, BAR            15.000   8.3131   5.0000   2.5000   1.6667   1.2500   1.0000
 T, K             2556.34  2278.85  2054.80  1776.91  1629.87  1532.39  1460.61
 RHO, KG/CU M    1.5254 0 9.4973-1 6.3384-1 3.6656-1 2.6643-1 2.1253-1 1.7838-1
 H, KJ/KG          263.72  -284.41  -707.16 -1216.17 -1481.11 -1655.63 -1783.78
 U, KJ/KG         -719.62 -1159.72 -1496.00 -1898.18 -2106.66 -2243.78 -2344.36
 G, KJ/KG        -28547.9 -25968.5 -23866.0 -21243.1 -19850.7 -18926.6 -18245.7
 S, KJ/(KG)(K)    11.2706  11.2706  11.2706  11.2706  11.2706  11.2706  11.2706

 M, (1/n)          21.615   21.647   21.658   21.662   21.663   21.663   21.663
 (dLV/dLP)t      -1.00114 -1.00040 -1.00014 -1.00003 -1.00001 -1.00001 -1.00001
 (dLV/dLT)p        1.0254   1.0096   1.0036   1.0007   1.0003   1.0001   1.0001
 Cp, KJ/(KG)(K)    2.0900   1.9388   1.8643   1.8114   1.7948   1.7872   1.7836
 GAMMAs            1.2382   1.2524   1.2614   1.2693   1.2722   1.2735   1.2742
 SON VEL,M/SEC     1103.4   1047.0    997.5    930.4    892.1    865.5    845.2
 MACH NUMBER        0.000    1.000    1.397    1.849    2.094    2.264    2.394

 PERFORMANCE PARAMETERS
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

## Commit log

2024-04-01 Added a CAD Folder
2024-04-01 Testing CAD.
2024-09-17 Add the procedure for using the NASA CEA, calculated the specific gas constant, Redid the NASA CEA at ideal pressures and O/F ratio.
2024-09-18 Finished the Requirements and Calculations Document for the Nozzle and Combustion Chamber
2024-09-18 Designed the combustion chamber and nozzle based on the calculations in the Requirements and Calculations Document
    [91290A154_Alloy Steel Socket Head Screw.SLDPRT, Combustion_Chamber.SLDPRT, Engine_Assembly.SLDASM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]
2024-09-18 Added Injector materials to read
2024-09-20 Added O-ring and the engine assembly to the CAD
    [Engine_Assembly.SLDASM, O-ring_2x39mm.SLDPRT]
2024-09-21 CAD Updates
    [91290A154_Alloy Steel Socket Head Screw.SLDPRT, 91290A180_Alloy Steel Socket Head Screw.SLDPRT, Combustion_Chamber.SLDPRT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]
2024-09-21 Small changes to the CAD
2024-09-23 completed injector plate
    [InjectorPlate.SLDPRT]
2024-10-01 Added a Plumbing BOM + Simulated Rocket Launch Profile with Current Specs
    [Plumbing_BOM.xlsx]
2024-10-03 More Plumbing stuff
    [316L-HDF4-500-SwagelokCompany-3D-09-30-2024.stp, Plumbing_BOM.xlsx]
2024-10-09 figured out what filetype it takes to import to ANSYS
    [Engine_Assembly - 91290A180_Alloy Steel Socket Head Screw-1.STL, Engine_Assembly - 91290A180_Alloy Steel Socket Head Screw-2.STL, Engine_Assembly - 91290A180_A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]
2024-10-10 Computations of comb chamb w/ inj plate. NO POST PROCESSING DONE
